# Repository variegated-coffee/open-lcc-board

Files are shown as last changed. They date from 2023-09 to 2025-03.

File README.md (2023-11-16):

# Open LCC Board

Schematics and PCB files for the main Open LCC hardware. Licensed under the CERN OHL-P license.

This is an evolution of [magnusnordlander/smart-lcc](https://github.com/magnusnordlander/smart-lcc).

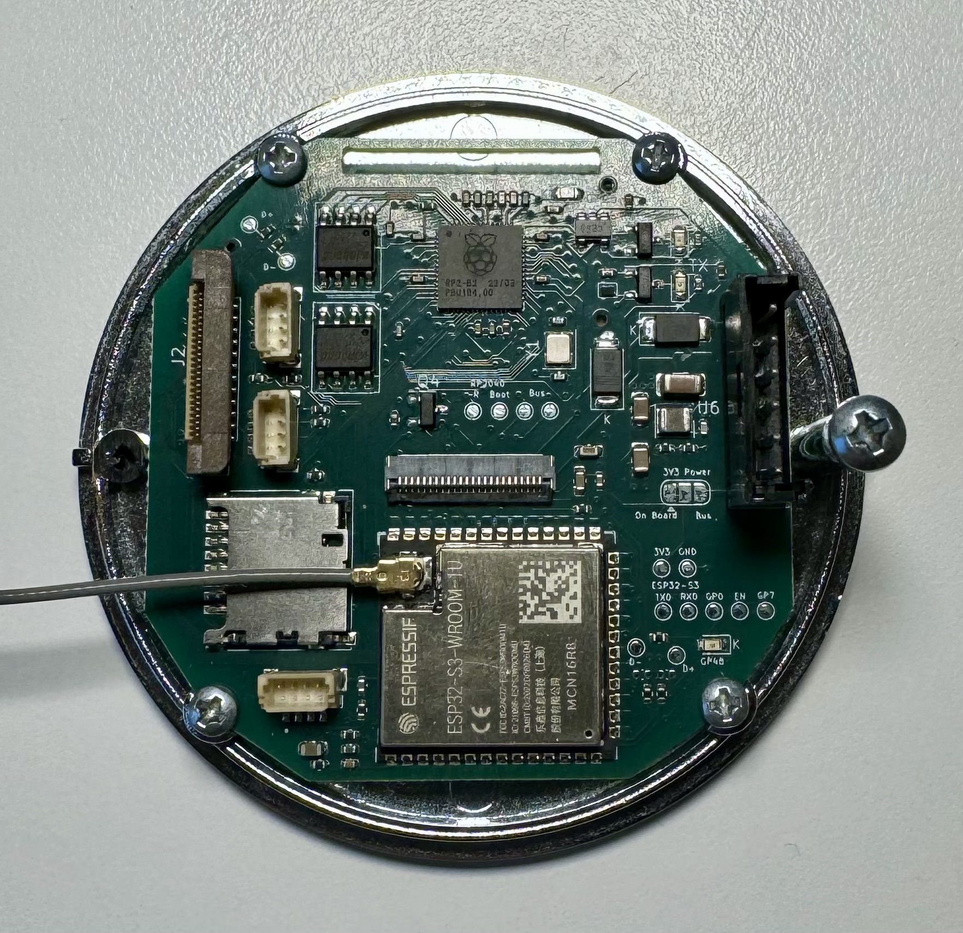
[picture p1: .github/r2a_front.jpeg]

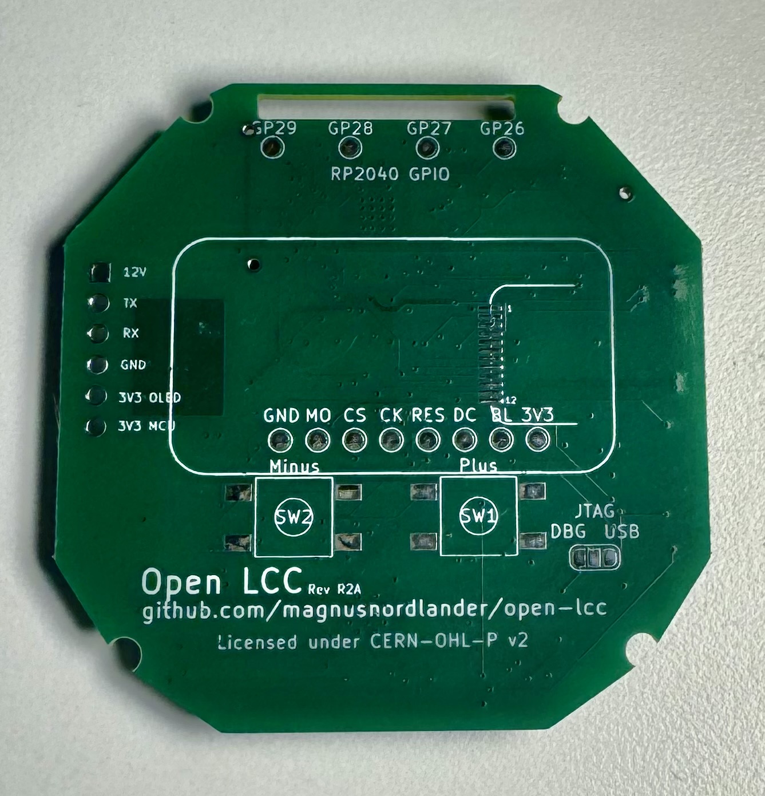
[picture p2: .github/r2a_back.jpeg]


## Disclaimer

Anything you do with this, you do at your own risk. Components have been fried already during the course of this project. Your machine uses both line voltage power, high pressured hot water, steam and other dangerous components. Risks include but are not limited to, damaging the machine, personal injury, property damage and summoning dead Cthulhu from his sleep at R'lyeh.

## Architecture and feature set

* RP2040 MCU communicating over UART with the Control Board
  * 2 MB Program Flash
  * 2 MB Settings Flash
  * Micro SD Card Slot
  * 2x QWIIC expansion ports
* ESP32-S3-WROOM-1U-N16R8 MCU
  * Connector for SSD1309 128x64px OLED display (only one display can be used at a time)
  * Solder pads for ST9987V 1.47" Round Rectangle TFT display (only one display can be used at a time)
  * Two push buttons
  * 1x QWIIC expansion port
  * Antenna connector (Espresso machines are basically faraday cages, so an external antenna is a good idea)
* 5 wire bus between RP2040 and ESP32-S3
	* RX, TX, CTS, RTS, Serial Boot
* Debug port
  * Exposes RP2040 USB, RP2040 SWD, RP2040 BOOTSEL, RP2040 ~RESET, ESP32 USB, ESP32 JTAG, ESP32 GPIO0, ESP32 EN and power rails.

## Hardware revisions

### Smart LCC (various revisions, not maintained in this repository)

The earliest revisions of this board. Based around Arduino RP2040 Nano.

### R1A (r1a branch)

This design is NOT RECOMMENDED for any purpose. It relies on the Control Board providing 3V3 to the board, but the Control Board is not able to supply enough power. As such, it *does not work as intended*. 

It is however a major redesign from the Smart LCC, and added most of the features described above.

### R2A (r2a branch)

Latest manufactured revision, though if you want one of the boards, you may want to wait for R2B.

#### Changes from R1A

* Added I2C pull-up resistors for QWIIC expansion ports
* Added on-board DC-DC converter to step down 12V to 3V3.
* Added back side connector for 1.47" TFT
* Moved test points for display connector to back side
* Added full bus to RP2040 settings flash (n.b. not the program flash), allowing for QSPI via PIO instead of regular SPI
* Added QWIIC expansion port to ESP32-S3
* Added Test Points for unused RP2040 GPIOs
* Removed 3V3_OLED from debug port

#### Errata

* The Schottky diodes do not provide adequate power supply reverse current protection. **DO NOT SUPPLY POWER FROM BOTH A DEBUG BOARD AND A CONTROL BOARD SIMULTANEOUSLY**
* It is unnecessary to connect both SD_DET_A and SD_DET_B to an MCU.

### R2B (r2b branch)

This revision hasn't been completely manufactured, and I don't intend to ever do that. I did order PCBs and verify the OR-ing controller subcircuit though, which is why there's now a R2C.

#### Changes from R2A

* Replaced the Schottky Diodes with two LM5050-1 OR-ing controllers.
* Connected SD card DET_A to GND, and removed the connection from the RP2040. 
* Widened traces and trace clearances, and added copper pours for improved manufacturability.

#### Errata

* The LM5050-1 and the MOSFET have reverse leakage currents totalling 0.6 mA. While this is unlikely to cause any issues in the real world, adding pulldown resistors seems prudent.

### R2C (main branch)

This revision hasn't been completely manufactured either (I'm running R2A in my machine), and as of writing, I don't have any plans to do so. Considering the small changes from R2B and R2A, which have been partially verified and fully verified respectively though, everything should work a treat.

#### Changes from R2B

* Added 18K7 pulldown resistors to the power supply rails.

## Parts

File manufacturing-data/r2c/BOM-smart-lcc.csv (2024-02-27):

Comment | Designator | Footprint | LCSC
18K7 | R26,R27 | R_0402_1005Metric | C102855
W25Q16JVSNIQ (Program Flash) | U4,U5 | SOIC-8_3.9x4.9mm_P1.27mm | C115407
BM04B-SRSS-TB(LF)(SN) | J4,J5,J8 | JST_BM04B-SRSS-TB(LF)(SN) | C160390
220R | R4 | R_0402_1005Metric | C160487
12 pF | C2,C7 | C_0402_1005Metric | C161527
910K | R1 | R_0402_1005Metric | C170371
RP2040 | U2 | QFN-56-1EP_7x7mm_P0.4mm_EP3.2x3.2mm | C2040
74LVC1G125 | U7 | SOT-23-5 | C23654
10K | R19,R21,R22,R9 | R_0402_1005Metric | C25744
1 uF, 16V | C11,C12,C23,C4,C8 | C_0402_1005Metric | C268023
10 μF, 25 V, X7R | C33 | C_1206_3216Metric | C2803388
TPZ3V6C-1006 | D3 | D_SOD-882_DFN1006-2 | C2923392
100R | R12,R2,R23,R3 | R_0402_1005Metric | C2935235
5.6 nF, 50V, C0G | C26 | C_0402_1005Metric | C2976066
22 uF, 10V, X5R | C28 | C_0603_1608Metric | C2980159
31K6 | R20 | R_0402_1005Metric | C2986236
ESP32-S3-WROOM-1 | U3 | ESP32-S3-WROOM-1U | C3013946
4K7 | R10,R11,R13,R15,R16,R17,R24,R25,R8 | R_0402_1005Metric | C3015810
27R | R5,R6 | R_0402_1005Metric | C321419
Conn_01x24 | J3 | FH34SRJ24S05SH50 | C324726
0R | R14,R7 | R_0402_1005Metric | C4288031
LM5050-1 | U1,U8 | TSOT-23-6 | C473393
TPS82130 | U6 | Texas_SIL0008D_MicroSiP-8-1EP_2.8x3mm_P0.65mm_EP1.1x1.9mm_ThermalVias | C473914
F0503-ZV-24-20T-R | J2 | Flexible24Pin | C481246
XYDBPCNANF-12MHZ | Y1 | Crystal_SMD_2520-4Pin_2.5x2.0mm | C521567
2.2 µF / 25V | C1,C3 | C_0603_1608Metric | C668356
Micro_SD_Card_Det2 | J6 | microSD_HC_Hirose_DM3D-SF | C719027
19-217/BHC-ZL1M2RY/3T | D1,D2,D4,D5 | LED_0603_1608Metric | C72041
NTGD3148NT1G | Q6 | TSOP-6_1.65x3.05mm_P0.95mm | C77713
22 uF, 10V, X7T | C25,C27 | C_0805_2012Metric | C782176
10R | R18 | R_0402_1005Metric | C851817
2N7002 | Q1,Q2,Q4 | SOT-23 | C8545
100 nF, 50V, X7R | C10,C13,C14,C15,C16,C17,C18,C19,C20,C21,C22,C24,C9 | C_0402_1005Metric | C960916

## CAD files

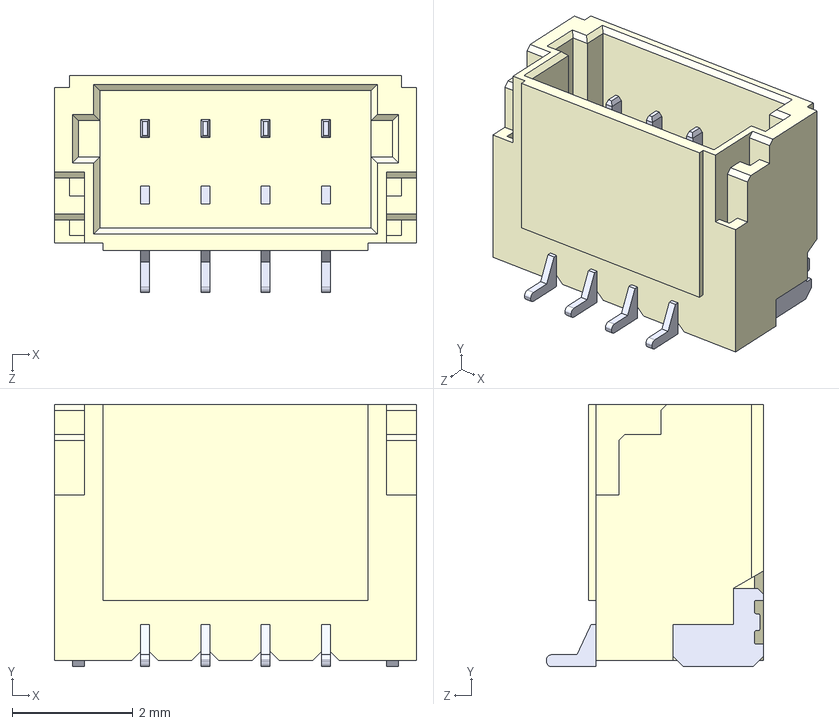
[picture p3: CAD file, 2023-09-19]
BM04B-SRSS-TB_LF__SN_/BM04B-SRSS-TB_LF__SN_.step
6.00 x 4.35 x 3.60 mm

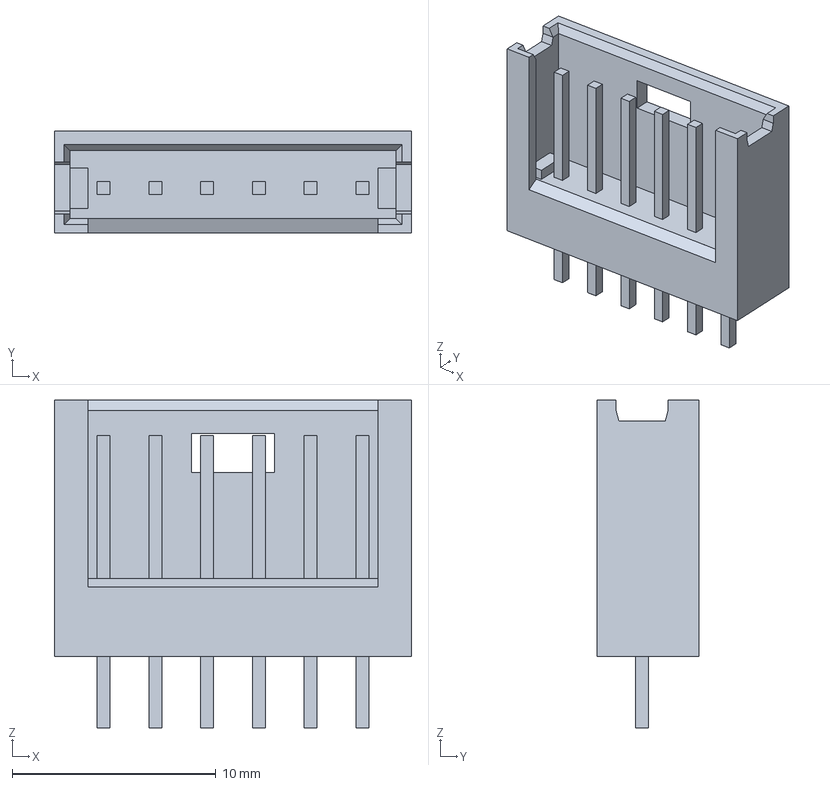
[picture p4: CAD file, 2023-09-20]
280372-1/280372-1.step
17.5 x 5.00 x 16.1 mm

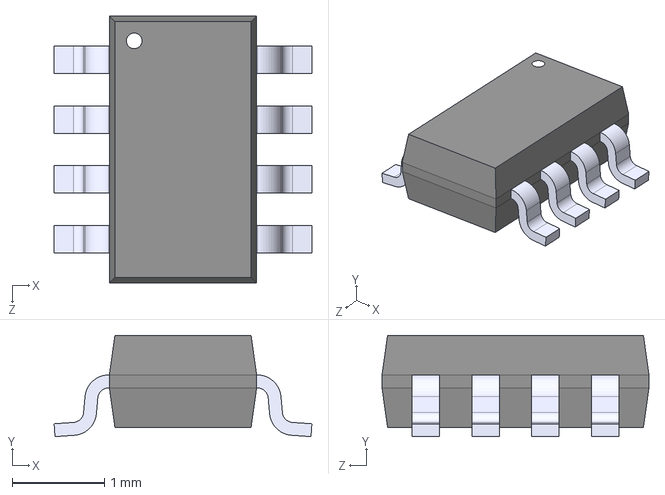
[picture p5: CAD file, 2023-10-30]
TPS562210ADDFR/TPS562210ADDFR.step
2.80 x 1.10 x 2.90 mm

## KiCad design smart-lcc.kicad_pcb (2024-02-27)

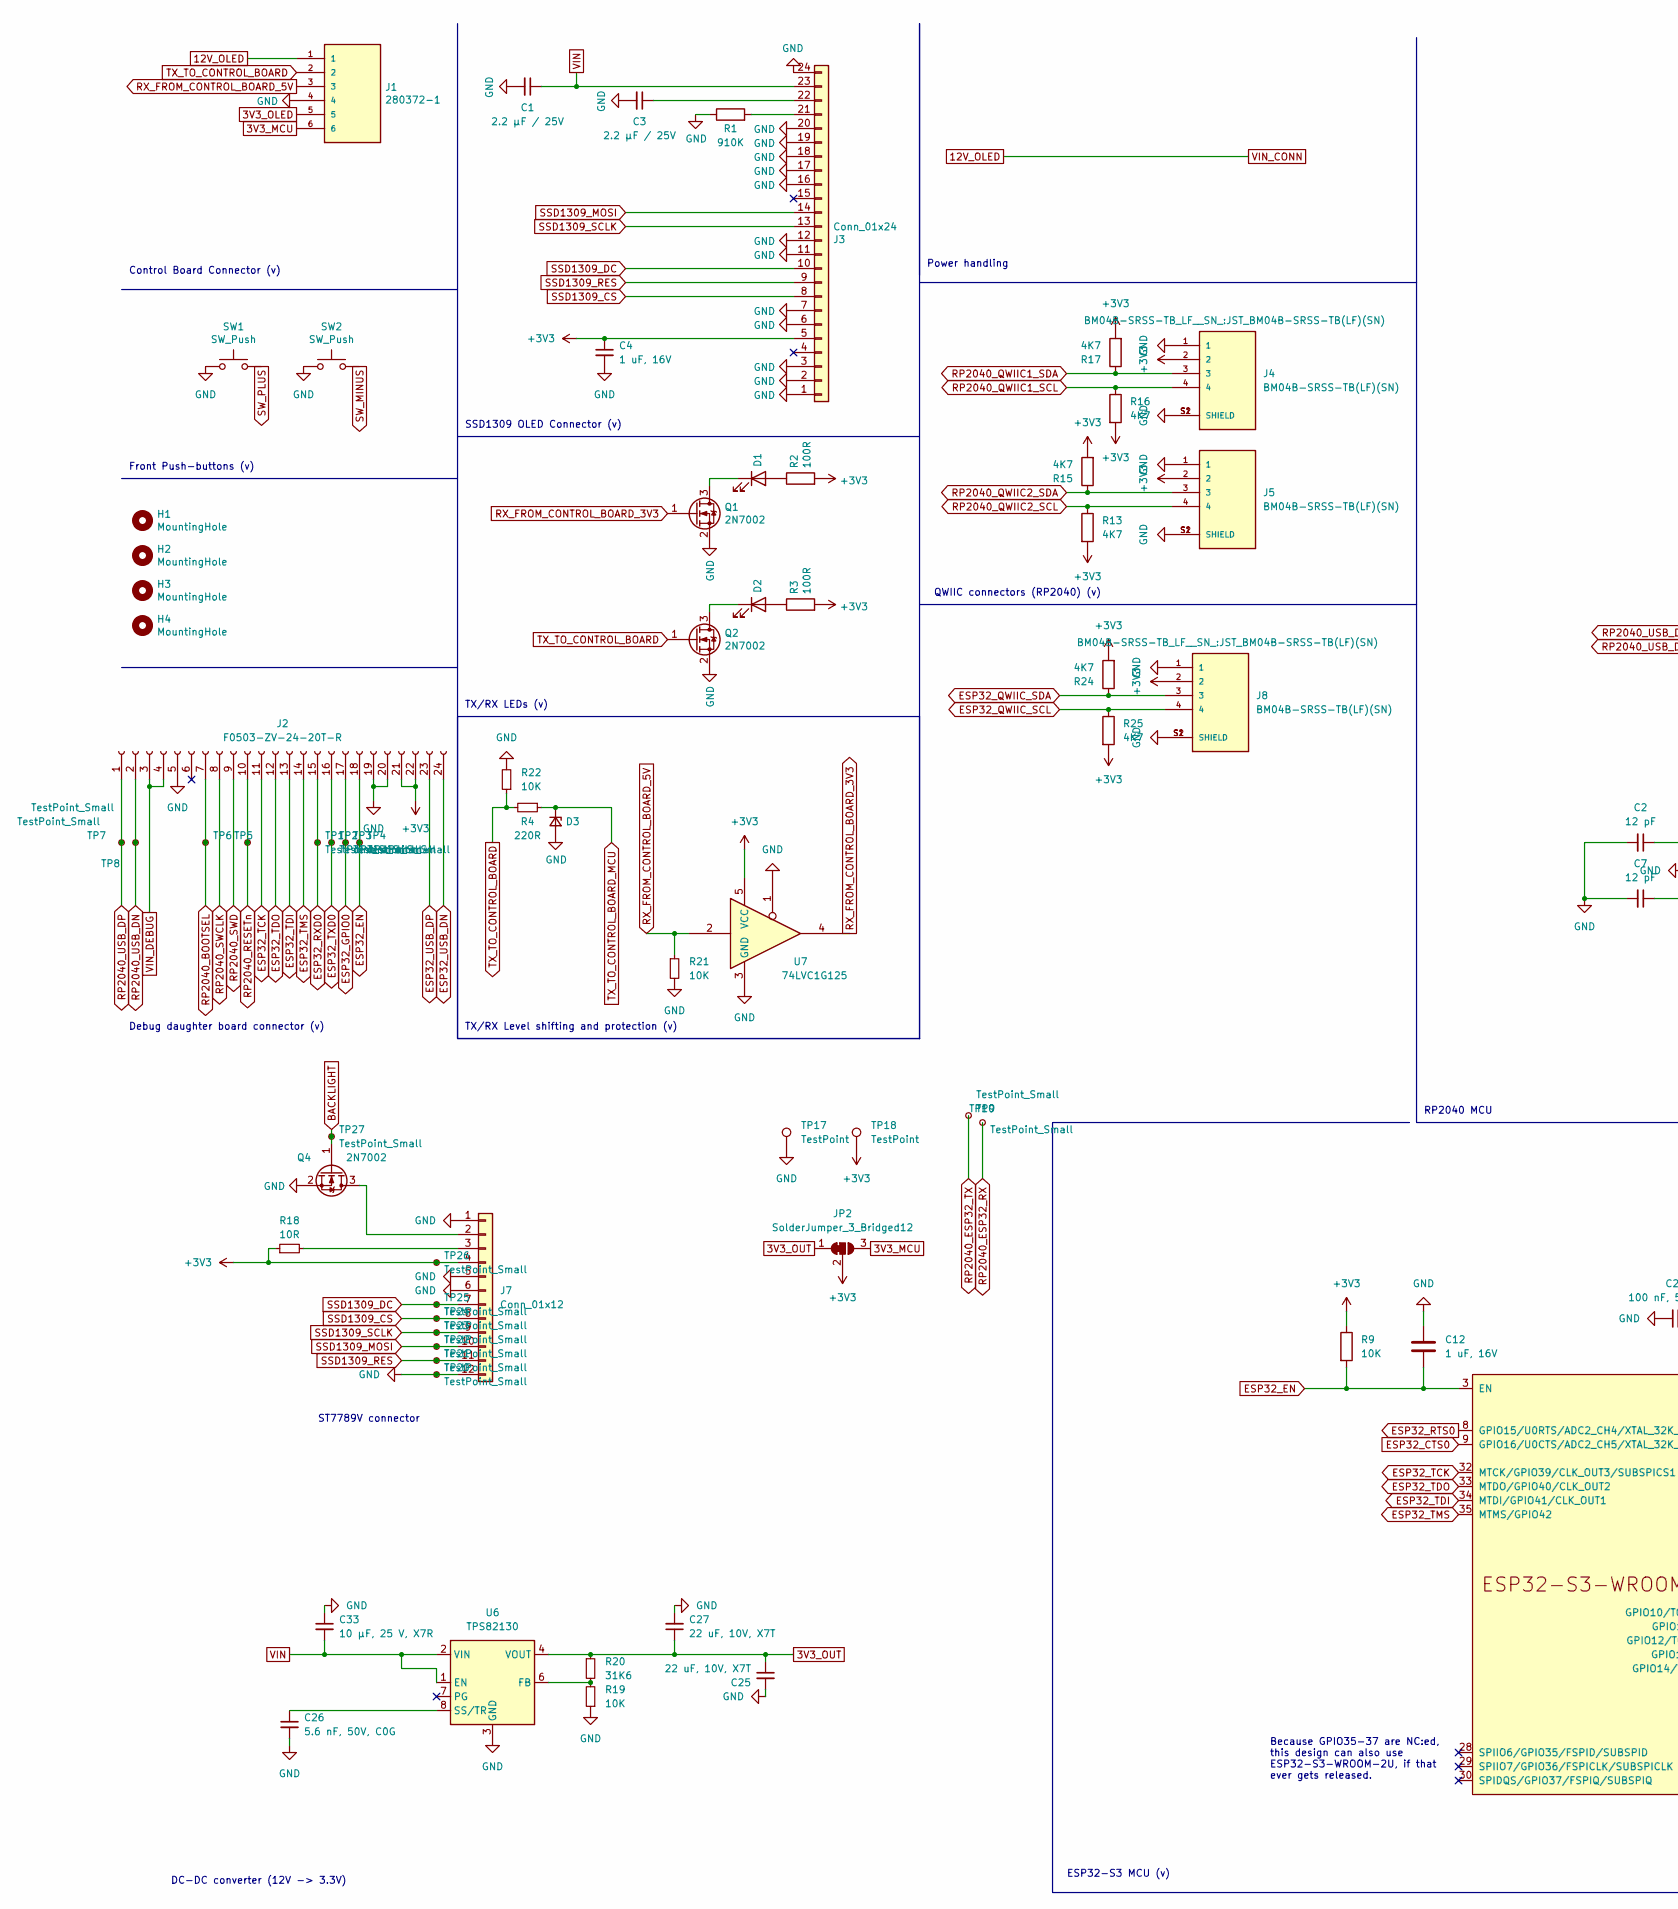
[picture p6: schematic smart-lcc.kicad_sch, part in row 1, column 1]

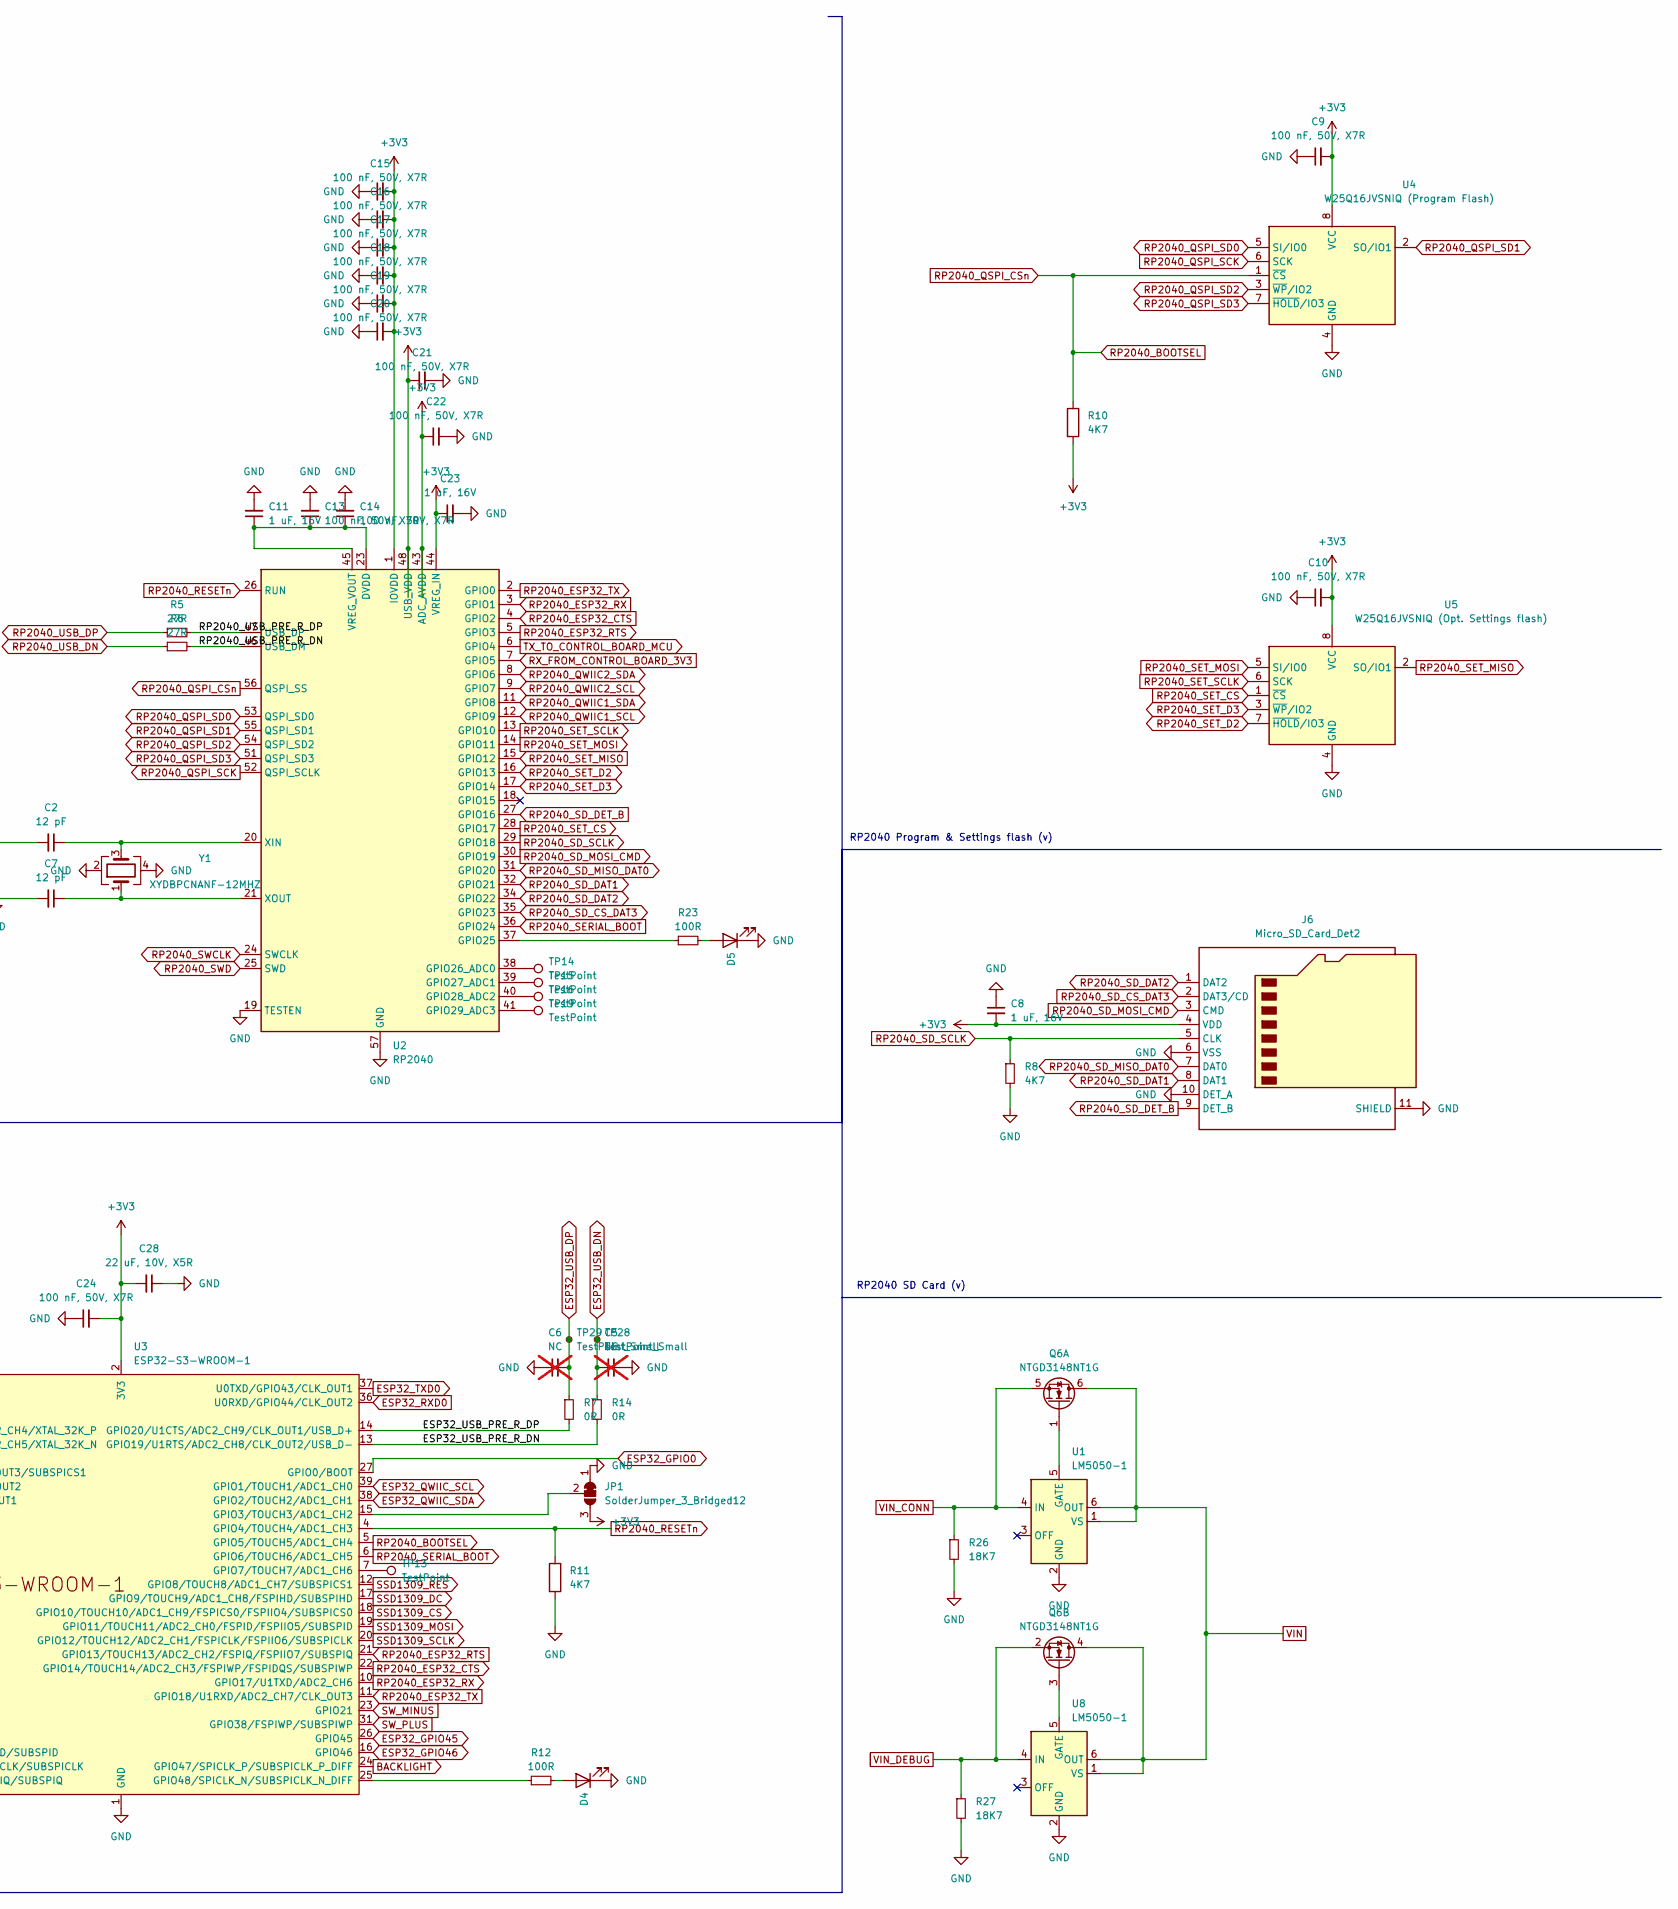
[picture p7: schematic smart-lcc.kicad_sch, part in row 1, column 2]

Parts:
C1, C3: 2.2 µF / 25V; C_0603_1608Metric; LCSC C668356
C2, C7: 12 pF; C_0402_1005Metric; LCSC C161527
C4, C8: 1 uF, 16V; C_0402_1005Metric; LCSC C268023
C5, C6: NC; C_0402_1005Metric; not fitted
C9, C10, C13, C14, C15, C16, C17, C18, C19, C20, C21, C22, C24: 100 nF, 50V, X7R; C_0402_1005Metric; JLCPCB Basic N
C11, C12, C23: 1 uF, 16V; C_0402_1005Metric; JLCPCB Basic N
C25, C27: 22 uF, 10V, X7T; C_0805_2012Metric; LCSC C782176
C26: 5.6 nF, 50V, C0G; C_0402_1005Metric; LCSC C2976066
C28: 22 uF, 10V, X5R; C_0603_1608Metric; LCSC C2980159
C33: 10 μF, 25 V, X7R; C_1206_3216Metric; LCSC C2803388
D1, D2, D4, D5: 19-217/BHC-ZL1M2RY/3T; LED_0603_1608Metric; JLCPCB Basic Y
D3: TPZ3V6C-1006; D_SOD-882_DFN1006-2; JLCPCB Basic N
H1, H2, H3, H4: MountingHole; MountingHole_2.7mm
J1: 280372-1; TE_280372-1
J2: F0503-ZV-24-20T-R; Flexible24Pin; JLCPCB Basic N
J3: Conn_01x24; FH34SRJ24S05SH50; JLCPCB Basic N
J4, J5, J8: BM04B-SRSS-TB(LF)(SN); JST_BM04B-SRSS-TB(LF)(SN); PARTREV N/A; LCSC C160390
J6: Micro_SD_Card_Det2; microSD_HC_Hirose_DM3D-SF; JLCPCB Basic N
J7: Conn_01x12; TFT_1.47IN_172X320_12P
JP1: SolderJumper_3_Bridged12; SolderJumper-3_P1.3mm_Bridged2Bar12_RoundedPad1.0x1.5mm_Num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
JP2: SolderJumper_3_Bridged12; SolderJumper-3_P1.3mm_Bridged2Bar12_RoundedPad1.0x1.5mm
Q1, Q2, Q4: 2N7002; SOT-23; JLCPCB Basic Y
Q6: NTGD3148NT1G; TSOP-6_1.65x3.05mm_P0.95mm; LCSC C77713
R1: 910K; R_0402_1005Metric; JLCPCB Basic N
R2, R3, R12, R23: 100R; R_0402_1005Metric; LCSC C2935235
R4: 220R; R_0402_1005Metric; JLCPCB Basic N
R5, R6: 27R; R_0402_1005Metric; LCSC C321419
R7, R14: 0R; R_0402_1005Metric; JLCPCB Basic N
R8, R10, R11, R13, R15, R16, R17, R24, R25: 4K7; R_0402_1005Metric; JLCPCB Basic N
R9: 10K; R_0402_1005Metric; JLCPCB Basic Y
R18: 10R; R_0402_1005Metric; LCSC C851817
R19, R21, R22: 10K; R_0402_1005Metric; LCSC C25744
R20: 31K6; R_0402_1005Metric; LCSC C2986236
R26, R27: 18K7; R_0402_1005Metric; LCSC C102855
SW1, SW2: SW_Push; ADTSMW65
TP1, TP2, TP3, TP4, TP5, TP6, TP7, TP8, TP9, TP10, TP28, TP29: TestPoint_Small; TestPoint_Pad_D1.0mm
TP13, TP17, TP18: TestPoint; TestPoint_Pad_D1.0mm
TP14, TP15, TP16, TP19: TestPoint; TestPoint_Pad_D1.5mm
TP20, TP21, TP22, TP23, TP24, TP25, TP26, TP27: TestPoint_Small; TestPoint_Pad_D1.5mm
U1, U8: LM5050-1; TSOT-23-6; LCSC C473393
U2: RP2040; QFN-56-1EP_7x7mm_P0.4mm_EP3.2x3.2mm; JLCPCB Basic N
U3: ESP32-S3-WROOM-1; ESP32-S3-WROOM-1U; JLCPCB Basic N
U4: W25Q16JVSNIQ (Program Flash); SOIC-8_3.9x4.9mm_P1.27mm; LCSC C115407
U5: W25Q16JVSNIQ (Opt. Settings flash); SOIC-8_3.9x4.9mm_P1.27mm; LCSC C115407
U6: TPS82130; Texas_SIL0008D_MicroSiP-8-1EP_2.8x3mm_P0.65mm_EP1.1x1.9mm_T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; LCSC C473914
U7: 74LVC1G125; SOT-23-5; LCSC C23654
Y1: XYDBPCNANF-12MHZ; Crystal_SMD_2520-4Pin_2.5x2.0mm; LCSC C521567

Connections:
3V3_MCU: J1.6, JP2.3 (B)
3V3_OLED: J1.5
3V3_OUT: C25.1, C27.1, JP2.1 (A), R20.1, U6.4 (VOUT), U6.5 (VOUT)
12V_OLED: J1.1, Q6.5 (S), R26.1, U1.4 (IN)
+3V3: C4.1, C8.2, C9.2, C10.2, C15.2, C16.2, C17.2, C18.2, C19.2, C20.2, C21.1, C22.1, C23.1, C24.2, C28.2, J2.21, J2.22, J3.5, J4.2, J5.2, J6.4 (VDD), J7.4, J8.2, JP1.3 (B), JP2.2 (C), R2.2, R3.2, R9.1, R10.2, R13.2, R15.2, R16.2, R17.2, R18.1, R24.2, R25.2, TP18.1, TP26.1, U2.1 (IOVDD), U2.10 (IOVDD), U2.22 (IOVDD), U2.33 (IOVDD), U2.42 (IOVDD), U2.43 (ADC_AVDD), U2.44 (VREG_IN), U2.48 (USB_VDD), U2.49 (IOVDD), U3.2 (3V3), U4.8 (VCC), U5.8 (VCC), U7.5 (VCC)
/ESP32_USB_PRE_R_DN: R14.2, U3.13 (GPIO19/U1RTS/ADC2_CH8/CLK_OUT2/USB_D-)
/ESP32_USB_PRE_R_DP: R7.2, U3.14 (GPIO20/U1CTS/ADC2_CH9/CLK_OUT1/USB_D+)
/RP2040_USB_PRE_R_DN: R6.2, U2.46 (USB_DM)
/RP2040_USB_PRE_R_DP: R5.2, U2.47 (USB_DP)
BACKLIGHT: Q4.1 (G), TP27.1, U3.24 (GPIO47/SPICLK_P/SUBSPICLK_P_DIFF)
ESP32_CTS0: U3.9 (GPIO16/U0CTS/ADC2_CH5/XTAL_32K_N)
ESP32_EN: C12.2, J2.18, R9.2, TP4.1, U3.3 (EN)
ESP32_GPIO0: J2.17, TP3.1, U3.27 (GPIO0/BOOT)
ESP32_GPIO45: U3.26 (GPIO45)
ESP32_GPIO46: U3.16 (GPIO46)
ESP32_QWIIC_SCL: J8.4, R25.1, U3.39 (GPIO1/TOUCH1/ADC1_CH0)
ESP32_QWIIC_SDA: J8.3, R24.1, U3.38 (GPIO2/TOUCH2/ADC1_CH1)
ESP32_RTS0: U3.8 (GPIO15/U0RTS/ADC2_CH4/XTAL_32K_P)
ESP32_RXD0: J2.15, TP1.1, U3.36 (U0RXD/GPIO44/CLK_OUT2)
ESP32_TCK: J2.11, U3.32 (MTCK/GPIO39/CLK_OUT3/SUBSPICS1)
ESP32_TDI: J2.13, U3.34 (MTDI/GPIO41/CLK_OUT1)
ESP32_TDO: J2.12, U3.33 (MTDO/GPIO40/CLK_OUT2)
ESP32_TMS: J2.14, U3.35 (MTMS/GPIO42)
ESP32_TXD0: J2.16, TP2.1, U3.37 (U0TXD/GPIO43/CLK_OUT1)
ESP32_USB_DN: C5.1, J2.24, R14.1, TP28.1
ESP32_USB_DP: C6.2, J2.23, R7.1, TP29.1
GND: C1.2, C2.2, C3.2, C4.2, C5.2, C6.1, C7.2, C8.1, C9.1, C10.1, C11.2, C12.1, C13.2, C14.2, C15.1, C16.1, C17.1, C18.1, C19.1, C20.1, C21.2, C22.2, C23.2, C24.1, C25.2, C26.2, C27.2, C28.1, C33.1, D3.2 (A), D4.1 (K), D5.1 (K), J1.4, J2.5, J2.19, J2.20, J3.1, J3.2, J3.3, J3.6, J3.7, J3.11, J3.12, J3.16, J3.17, J3.18, J3.19, J3.20, J3.24, J4.1, J4.S1 (SHIELD), J4.S2 (SHIELD), J5.1, J5.S1 (SHIELD), J5.S2 (SHIELD), J6.6 (VSS), J6.10 (DET_A), J6.11 (SHIELD), J7.1, J7.5, J7.6, J7.12, J8.1, J8.S1 (SHIELD), J8.S2 (SHIELD), JP1.1 (A), Q1.2 (S), Q2.2 (S), Q4.2 (S), R1.1, R8.2, R11.2, R19.1, R21.2, R22.2, R26.2, R27.2, SW1.1, SW2.1, TP17.1, TP20.1, U1.2 (GND), U2.19 (TESTEN), U2.57 (GND), U3.1 (GND), U3.40 (GND), U3.41 (GND), U4.4 (GND), U5.4 (GND), U6.3 (GND), U6.9 (GND), U7.1, U7.3 (GND), U8.2 (GND), Y1.2, Y1.4
unnamed: D1.2 (A), R2.1
unnamed: D1.1 (K), Q1.3 (D)
unnamed: D2.2 (A), R3.1
unnamed: D2.1 (K), Q2.3 (D)
unnamed: D4.2 (A), R12.2
unnamed: D5.2 (A), R23.2
unnamed: J3.21, R1.2
unnamed: C3.1, J3.22
unnamed: J7.2, Q4.3 (D)
unnamed: J7.3, R18.2
unnamed: JP1.2 (C), U3.15 (GPIO3/TOUCH3/ADC1_CH2)
unnamed: Q6.1 (G), U1.5 (GATE)
unnamed: Q6.3 (G), U8.5 (GATE)
unnamed: R23.1, U2.37 (GPIO25)
unnamed: TP14.1, U2.38 (GPIO26_ADC0)
unnamed: TP15.1, U2.39 (GPIO27_ADC1)
unnamed: TP16.1, U2.40 (GPIO28_ADC2)
unnamed: TP19.1, U2.41 (GPIO29_ADC3)
unnamed: C11.1, C13.1, C14.1, U2.23 (DVDD), U2.45 (VREG_VOUT), U2.50 (DVDD)
unnamed: C2.1, U2.20 (XIN), Y1.3
unnamed: C7.1, U2.21 (XOUT), Y1.1
unnamed: TP13.1, U3.7 (GPIO7/TOUCH7/ADC1_CH6)
unnamed: R12.1, U3.25 (GPIO48/SPICLK_N/SUBSPICLK_N_DIFF)
unnamed: R19.2, R20.2, U6.6 (FB)
unnamed: C26.1, U6.8 (SS/TR)
RP2040_BOOTSEL: J2.7, R10.1, TP6.1, U2.56 (QSPI_SS), U3.5 (GPIO5/TOUCH5/ADC1_CH4), U4.1 (~CS)
RP2040_ESP32_CTS: U2.4 (GPIO2), U3.22 (GPIO14/TOUCH14/ADC2_CH3/FSPIWP/FSPIDQS/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)
RP2040_ESP32_RTS: U2.5 (GPIO3), U3.21 (GPIO13/TOUCH13/ADC2_CH2/FSPIQ/FSPIIO7/S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)
RP2040_ESP32_RX: TP9.1, U2.3 (GPIO1), U3.10 (GPIO17/U1TXD/ADC2_CH6)
RP2040_ESP32_TX: TP10.1, U2.2 (GPIO0), U3.11 (GPIO18/U1RXD/ADC2_CH7/CLK_OUT3)
RP2040_QSPI_SCK: U2.52 (QSPI_SCLK), U4.6 (SCK)
RP2040_QSPI_SD0: U2.53 (QSPI_SD0), U4.5 (SI/IO0)
RP2040_QSPI_SD1: U2.55 (QSPI_SD1), U4.2 (SO/IO1)
RP2040_QSPI_SD2: U2.54 (QSPI_SD2), U4.3 (~WP/IO2)
RP2040_QSPI_SD3: U2.51 (QSPI_SD3), U4.7 (~HOLD/IO3)
RP2040_QWIIC1_SCL: J4.4, R16.1, U2.12 (GPIO9)
RP2040_QWIIC1_SDA: J4.3, R17.1, U2.11 (GPIO8)
RP2040_QWIIC2_SCL: J5.4, R13.1, U2.9 (GPIO7)
RP2040_QWIIC2_SDA: J5.3, R15.1, U2.8 (GPIO6)
RP2040_RESETn: J2.10, R11.1, TP5.1, U2.26 (RUN), U3.4 (GPIO4/TOUCH4/ADC1_CH3)
RP2040_SD_CS_DAT3: J6.2 (DAT3/CD), U2.35 (GPIO23)
RP2040_SD_DAT1: J6.8 (DAT1), U2.32 (GPIO21)
RP2040_SD_DAT2: J6.1 (DAT2), U2.34 (GPIO22)
RP2040_SD_DET_B: J6.9 (DET_B), U2.27 (GPIO16)
RP2040_SD_MISO_DAT0: J6.7 (DAT0), U2.31 (GPIO20)
RP2040_SD_MOSI_CMD: J6.3 (CMD), U2.30 (GPIO19)
RP2040_SD_SCLK: J6.5 (CLK), R8.1, U2.29 (GPIO18)
RP2040_SERIAL_BOOT: U2.36 (GPIO24), U3.6 (GPIO6/TOUCH6/ADC1_CH5)
RP2040_SET_CS: U2.28 (GPIO17), U5.1 (~CS)
RP2040_SET_D2: U2.16 (GPIO13), U5.7 (~HOLD/IO3)
RP2040_SET_D3: U2.17 (GPIO14), U5.3 (~WP/IO2)
RP2040_SET_MISO: U2.15 (GPIO12), U5.2 (SO/IO1)
RP2040_SET_MOSI: U2.14 (GPIO11), U5.5 (SI/IO0)
RP2040_SET_SCLK: U2.13 (GPIO10), U5.6 (SCK)
RP2040_SWCLK: J2.8, U2.24 (SWCLK)
RP2040_SWD: J2.9, U2.25 (SWD)
RP2040_USB_DN: J2.2, R6.1, TP8.1
RP2040_USB_DP: J2.1, R5.1, TP7.1
RX_FROM_CONTROL_BOARD_3V3: Q1.1 (G), U2.7 (GPIO5), U7.4
RX_FROM_CONTROL_BOARD_5V: J1.3, R21.1, U7.2
SSD1309_CS: J3.8, J7.8, TP24.1, U3.18 (GPIO10/TOUCH10/ADC1_CH9/FSPICS0/FSPIIO4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)
SSD1309_DC: J3.10, J7.7, TP25.1, U3.17 (GPIO9/TOUCH9/ADC1_CH8/FSPIHD/SUBSPIHD)
SSD1309_MOSI: J3.14, J7.10, TP22.1, U3.19 (GPIO11/TOUCH11/ADC2_CH0/FSPID/FSPIIO5/S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)
SSD1309_RES: J3.9, J7.11, TP21.1, U3.12 (GPIO8/TOUCH8/ADC1_CH7/SUBSPICS1)
SSD1309_SCLK: J3.13, J7.9, TP23.1, U3.20 (GPIO12/TOUCH12/ADC2_CH1/FSPICLK/FSPIIO6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)
SW_MINUS: SW2.2, U3.23 (GPIO21)
SW_PLUS: SW1.2, U3.31 (GPIO38/FSPIWP/SUBSPIWP)
TX_TO_CONTROL_BOARD: J1.2, Q2.1 (G), R4.2, R22.1
TX_TO_CONTROL_BOARD_MCU: D3.1 (K), R4.1, U2.6 (GPIO4)
VIN: C1.1, C33.2, J3.23, Q6.4 (D), Q6.6 (D), U1.1 (VS), U1.6 (OUT), U6.1 (EN), U6.2 (VIN), U8.1 (VS), U8.6 (OUT)
VIN_DEBUG: J2.3, J2.4, Q6.2 (S), R27.1, U8.4 (IN)

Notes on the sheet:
Power handling
RP2040 Program & Settings flash (v)
TX/RX LEDs (v)
RP2040 MCU
TX/RX Level shifting and protection (v)
DC-DC converter (12V -> 3.3V)
ESP32-S3 MCU (v)
ST7789V connector
Control Board Connector (v)
RP2040 SD Card (v)
Front Push-buttons (v)
SSD1309 OLED Connector (v)
Because GPIO35-37 are NC:ed, this design can also use ESP32-S3-WROOM-2U, if that ever gets released.
Debug daughter board connector (v)
QWIIC connectors (RP2040) (v)

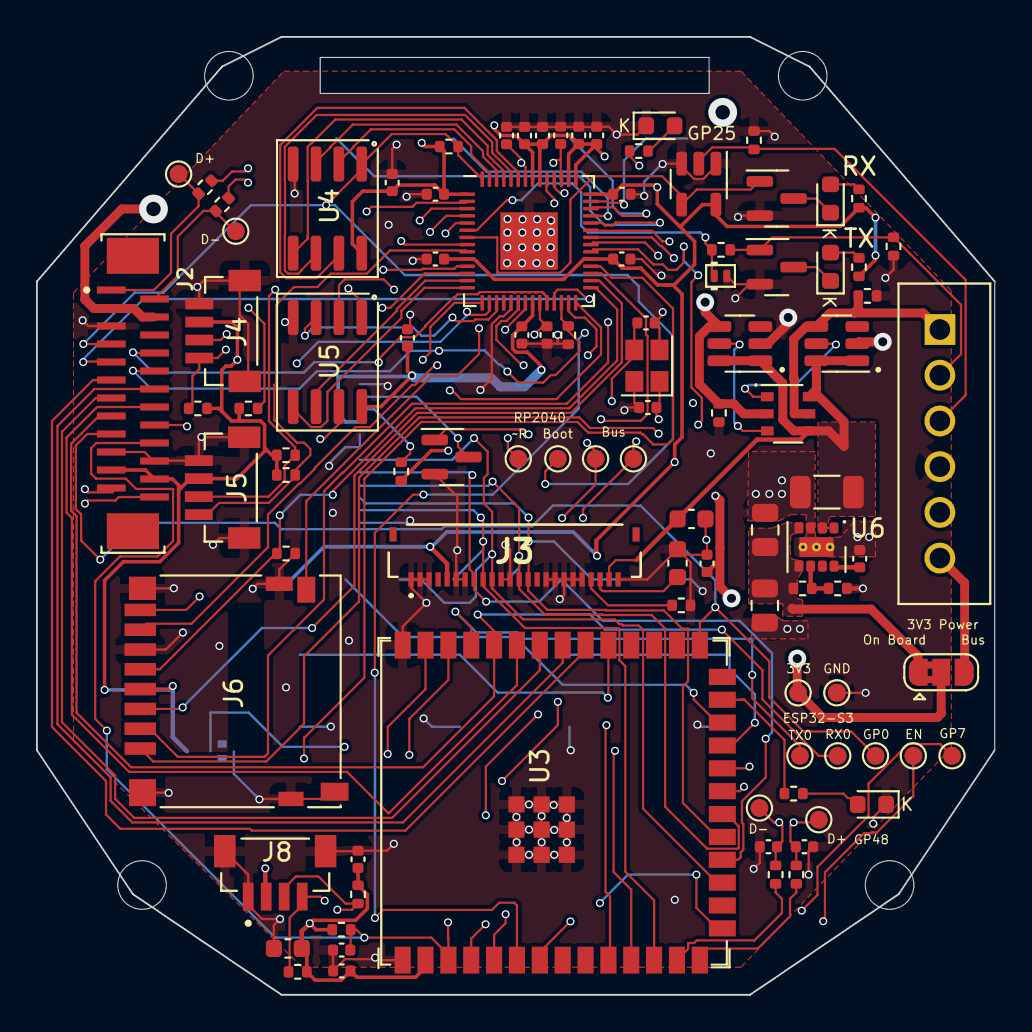
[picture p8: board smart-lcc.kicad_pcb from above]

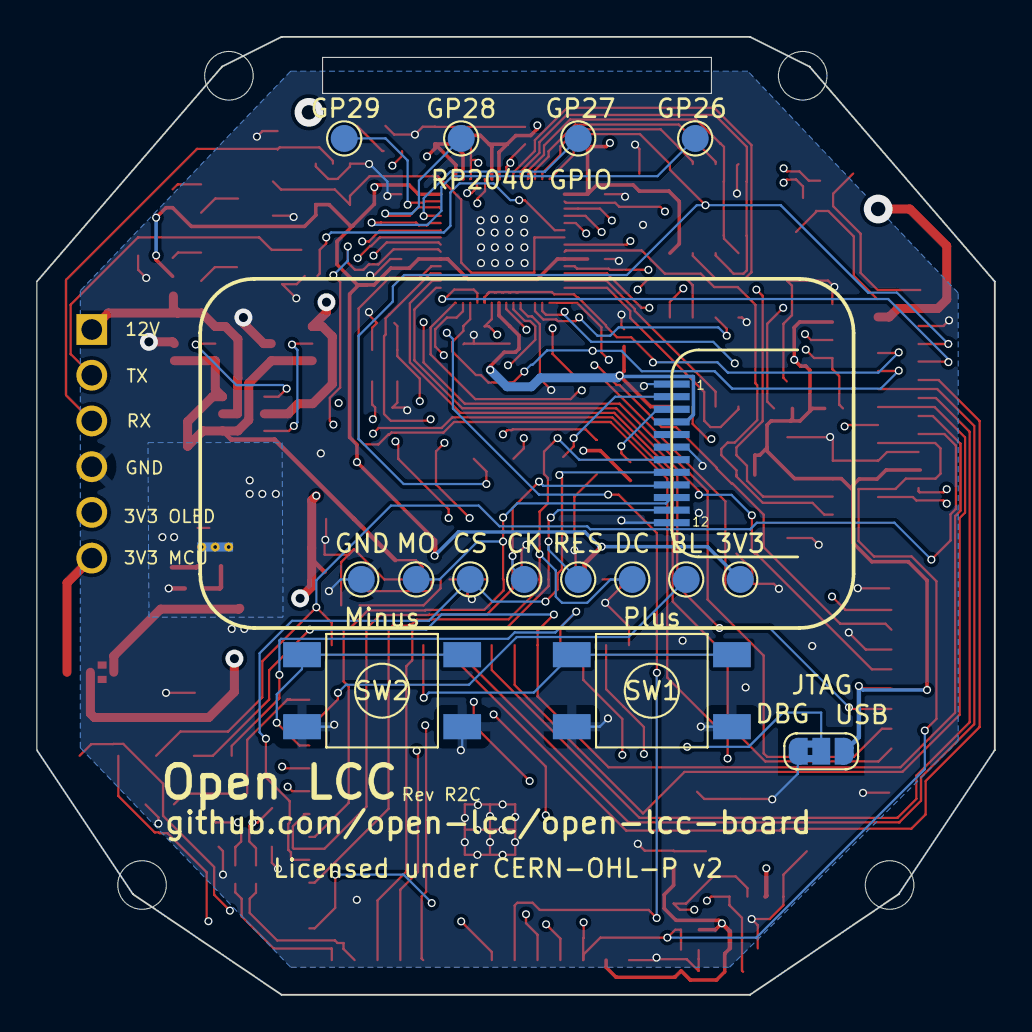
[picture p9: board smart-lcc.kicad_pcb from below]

Board: 4 copper layers, 53.2 x 53.2 mm, 117 parts (16 on the bottom side), 93 nets.

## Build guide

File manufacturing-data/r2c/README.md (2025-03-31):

# How to order and assemble

## PCB and PCBA manufacturer

This directory contains Gerber files for the PCB, a BOM file with LCSC numbers for ordering with JLCPCB, and a CPL file. When ordering, it's *highly* recommended to also order a debug board. It is possible to flash the boards without one, but you'll have to solder on a USB cable to test points.

### Orientations

Be careful with the orientation of the debug board FPC connector. Pin 1 is indicated on the board. When placed correctly on both the Open LCC and Debug board, you should use an FPC cable with *connectors on opposite sides*. If for some reason the connector is incorrectly oriented, you'll still be able to use the boards, but you may need an FPC cable with connectors on the *same* side. 

If you have _any_ doubt as to the orientation of the connector, it's a good idea to check for continuity between e.g. the USB D+/D- pins on the main board, and the D+/D- pins of the USB connector of the debug board *before applying power*. Applying power with reversed polarity can fry your board. 

Orientations in general are a bit of a pain. I recommend checking the "Confirm production files" option on JLCPCB, to be able to verify that the orientations of all the components match the PCB and schematic.

## Parts you'll need from other vendors

The BOM in the file isn't complete; you'll need a few other parts, some of which are hand soldered. Below is a table, including links to Digikey when the item is available there.

Of special note is the display. You can use either a Color TFT or an OLED. The OLED matches what's in the stock LCC, and is easy to install. The TFT requires some soldering skills to install, but is a lot higher resolution. Pick one. Also, at least the OLED (or rather a compatible one) is also available on Digikey, but it's *a lot* more expensive than on AliExpress.

| Designator  | Part name | Notes | URL (for one vendor, usually there are others) |
|---|---|---|---|
| J1 | TE 280372-1 | You *can* use a standard 2.54 mm pin header instead, but this is highly recommended. | https://www.digikey.se/en/products/detail/te-connectivity-amp-connectors/280372-1/2276004 |
| SW1, SW2 | Omron B3S-1000 | | https://www.digikey.se/en/products/detail/omron-electronics-inc-emc-div/B3S-1000/20686 |
| J7 | CH147QV01A | This is the Color TFT. Buy either this, or the OLED display, not both. Don't get the module, get the bare screen. | https://aliexpress.com/item/1005003771379232.html |
| - | WEO012864A | This is the OLED. There are a *lot* of different manufacturers for this. Make sure the pinout and pitch matches.  | https://aliexpress.com/item/1005003108880951.html |
| - | 05-24-D-0203-A-4-06-4-T | FPC cable to connect to Debug board | https://www.digikey.se/en/products/detail/gct/05-24-D-0203-A-4-06-4-T/21266839 |
| - | AFAG2220-SW2 | WiFi/Bluetooth Antenna (220 mm cable) | https://www.digikey.se/en/products/detail/abracon-llc/AFAG2220-SW2/9603584 |

## Assembly

J1, SW1 and SW2 need to be soldered on. These are fairly easy to solder by hand, but be careful with the orientation of J1. It needs to match the orientation of the same header on the stock LCC. If you're using the TFT, that also needs to be soldered on, after which you should put kapton tape on the connector. You'll need to use double sided tape to attach the display to the board, but I'd recommend using a fairly tiny pad of it. That way, if your display is crooked, you'll probably be able to remove it without destroying it (speaking from experience).

The easiest way to flash the boards is with the debug board, which contains Micro-USB connectors for both the RP2040 and the ESP32-S3. It also has push-buttons for reset, RP2040 bootsel, and ESP32 GPIO0. Like I said, highly recommended.

Once everything is flashed, the board is ready to be installed.

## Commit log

2023-10-30 R2A WIP
    [TPS562210ADDFR.step, smart-lcc.kicad_pcb, smart-lcc.kicad_sch]
2023-10-30 Initial work on R2B
    [smart-lcc.kicad_pcb, smart-lcc.kicad_sch]
2023-10-31 Removed SD_DET_A from RP2040 and connected DET_A on the SD card to GND
    [smart-lcc.kicad_pcb, smart-lcc.kicad_sch]
2023-11-03 Updated design for easier manufacturability
    [smart-lcc.kicad_pcb, smart-lcc.kicad_sch]
2023-11-09 Add board photos
2023-11-16 Added revision R2C
    [smart-lcc.kicad_pcb, smart-lcc.kicad_sch]
2023-11-16 Silk screen changes
    [smart-lcc.kicad_pcb]
2024-02-24 Added some very basic ordering information (more soon)
    [BOM-smart-lcc.csv, smart-lcc.kicad_pcb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]
2024-02-27 Updated to use a more flexible FPC connector footprint
    [BOM-smart-lcc.csv, smart-lcc.kicad_pcb, smart-lcc.kicad_sch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]

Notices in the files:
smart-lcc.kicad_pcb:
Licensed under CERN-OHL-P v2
